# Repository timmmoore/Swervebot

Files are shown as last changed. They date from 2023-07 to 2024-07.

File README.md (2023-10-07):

# Swervebot

https://cad.onshape.com/documents/ee819cf6ea491e04f0fba739/w/47ab37900572e080b95199d2/e/a63b98e65827662d9141c87c

https://cad.onshape.com/documents/98357d3c8f8b098add8002f2/w/b5a1efd9deb641ade0f32837/e/772a9ea7ca7ad6a00d48e67d

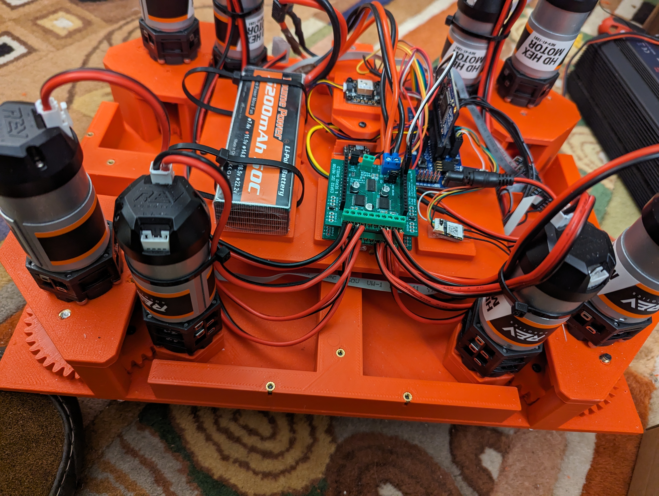
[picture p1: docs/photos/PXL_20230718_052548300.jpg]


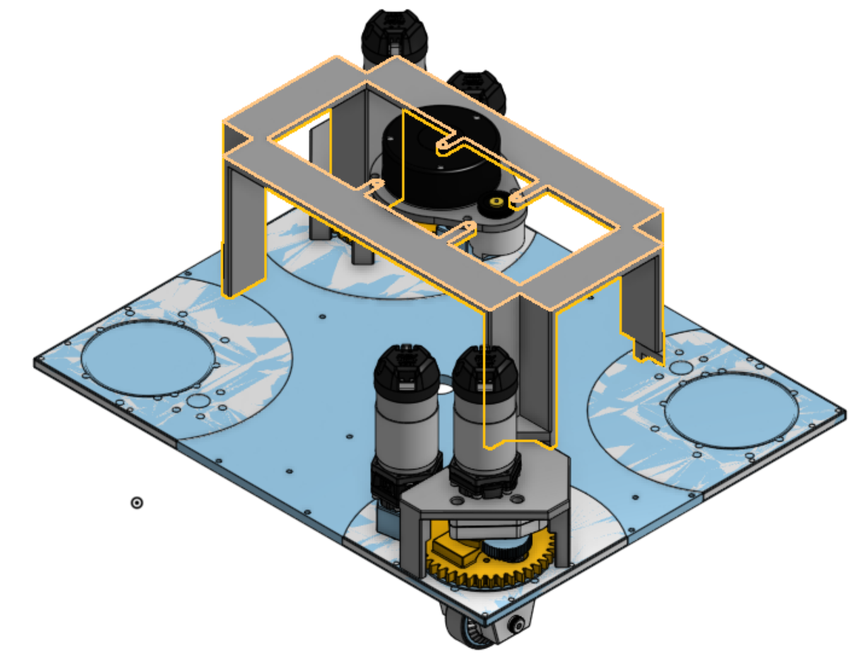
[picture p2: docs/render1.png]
render


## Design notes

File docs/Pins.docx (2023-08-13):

# Pins

SBUS_RX | 7 | Channel data from receiver
S.PORT | 6 | Telemetry to transmitter
SBUS_TX (not used) | 5 | Backup SBUS from 2nd Rx
MOTOR_SDA | 23 | 1MHz I2C for 2 motor drivers 0x40, 0x41
MOTOR_SCL | 22
MOTOR DRIVER FAN | 30
ENCODER1 | 8 | PWM SRX through bore encoder
ENCODER2 | 9
ENCODER3 | 10
ENCODER4 | 11
QUADRATURE 1A | 15 | Encoder on drive motors
QUADRATURE 1B | 14
QUADRATURE 2A | 3
QUADRATURE 2B | 2
QUADRATURE 3A | 13
QUADRATURE 3B | 12
QUADRATURE 4A | 1
QUADRATURE 5B | 0
PMW CS | 19 | Pmw3901 optical flow sensor, SPI
PMW SCK | 18
PMW SDO | 17
PMW SDI | 16
USFSMAX SDA | 21 | 3.4MHz I2C for IMU 0x57
USFSMAX SCL | 20
USFSMAX RESET | -1 | Not used
BATTERY ANALOG | 31 | ADC, resistor divider 8K2+3K
TEMP1 ANALOG | 26 | TMP36 temperature sensors on ADC
TEMP2 ANALOG | 27
TEMP3 ANALOG | 28
TEMP4 ANALOG | 29
GPS SDA | 24 | 1.5MHz I2C 0x10
GPS SCL | 25
SPARE2 | 4
WIFI_RES | 56 | WIFI connection for programming/debug
WIFI_PGM | 57
DEBUG_TX/WIFI_DI | 62
DEBUG_RX/WIFI_DO | 63
SD SDO | 58
SD SDI | 59
SD CS | 60
SD CLK | 61

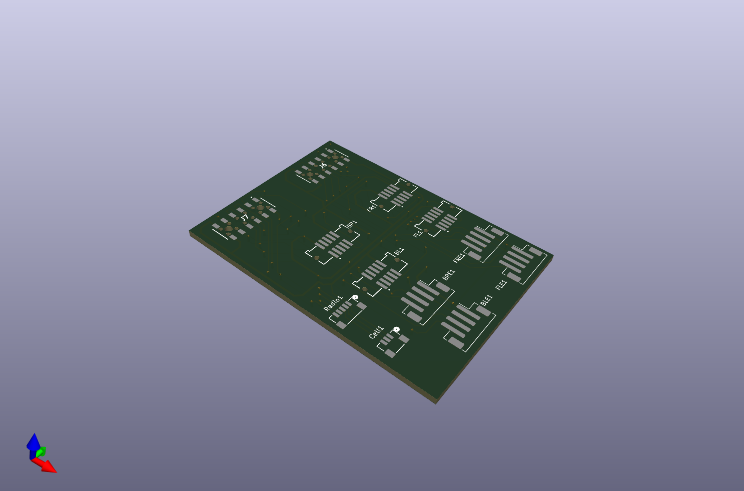
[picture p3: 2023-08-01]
docs/sensor2.png

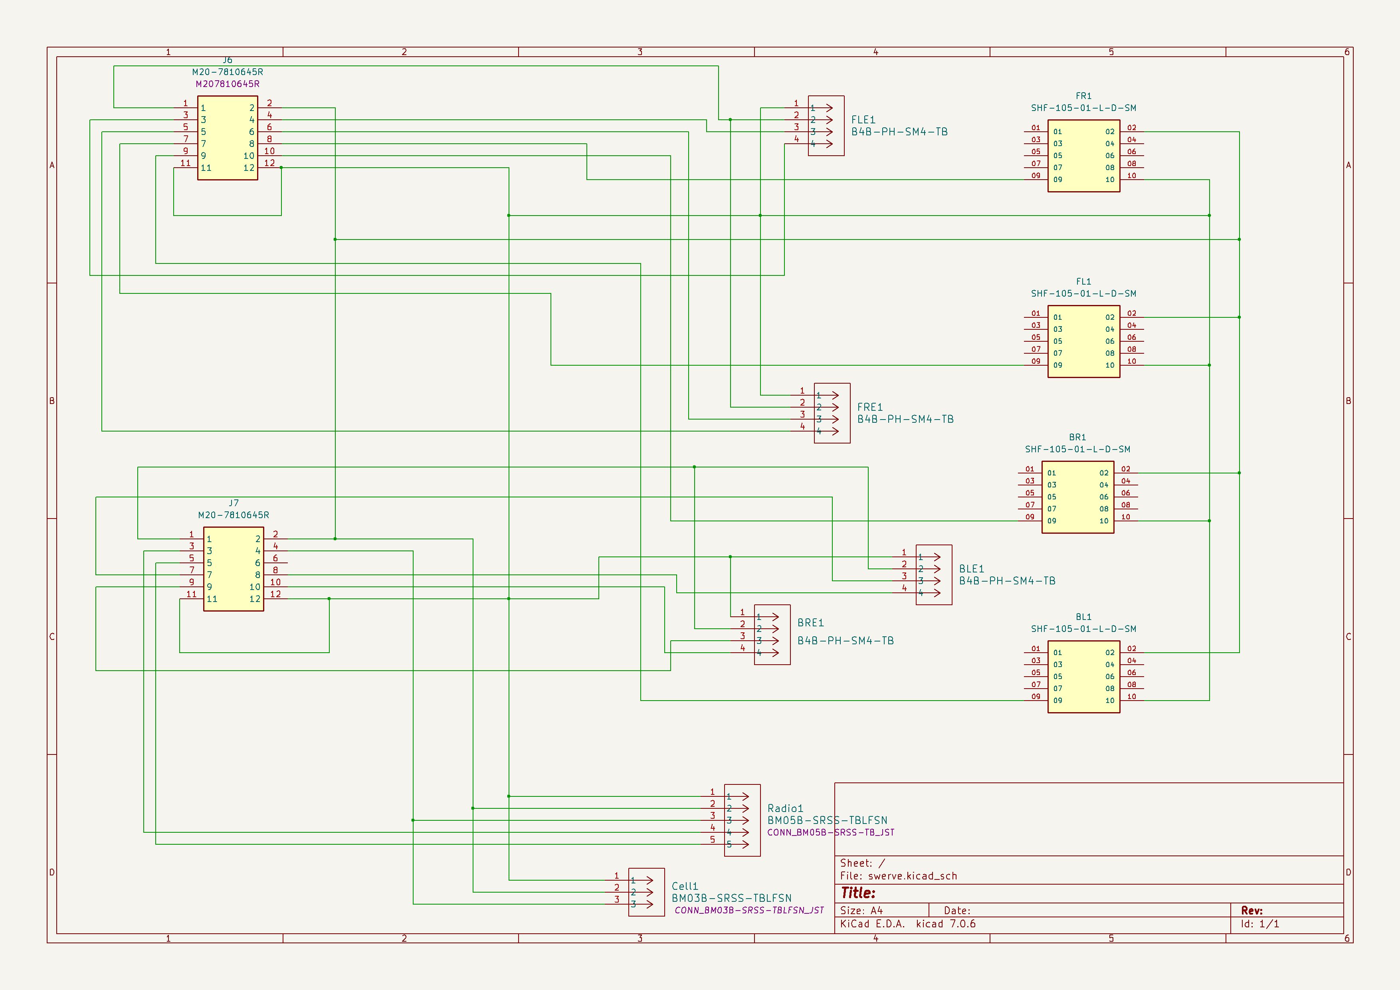
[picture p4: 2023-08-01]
docs/sensorsch2.png

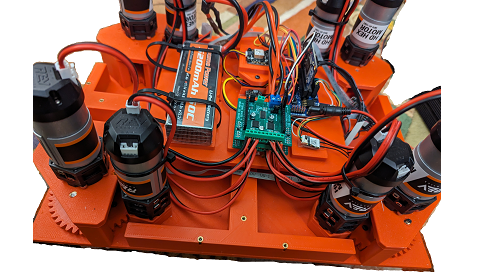
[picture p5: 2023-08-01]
docs/photos/swerve1.png

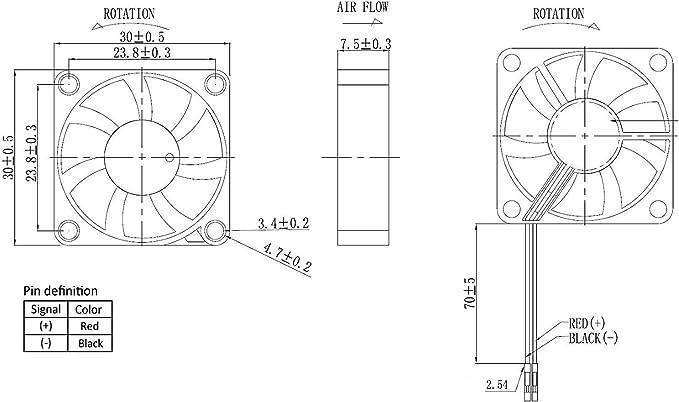
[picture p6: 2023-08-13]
docs/615SG+HSIiL._AC_SX679_.jpg

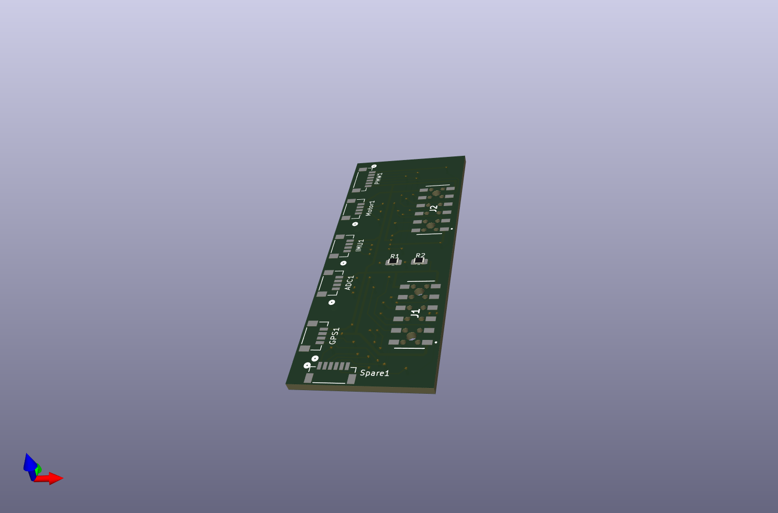
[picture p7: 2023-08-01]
docs/sensor1.png

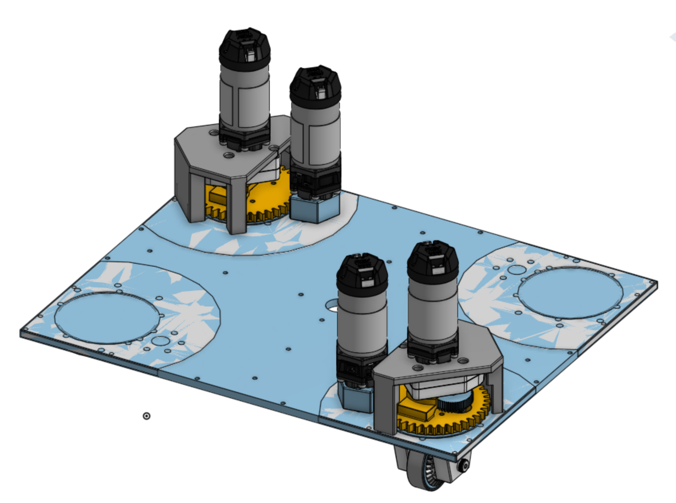
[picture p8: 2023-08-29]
docs/render.png

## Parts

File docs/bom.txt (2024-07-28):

8x	motors			https://www.revrobotics.com/rev-41-1600/						$360
1x	bearing insert		https://www.revrobotics.com/rev-41-1528-pk20/						$10
4x	12 tooth gear		https://www.revrobotics.com/5mm-Metal-Hex-Bore-Gears/					$20
4x	through bore encoder	https://www.revrobotics.com/rev-11-1271/						$192

4x	bevel gear		https://www.gobilda.com/2-1-ratio-bevel-gear-set-8mm-rex-bore-pinion-gear/		$120
4x	gear			https://www.gobilda.com/2303-series-steel-mod-0-8-pinion-gear-8mm-rex-bore-30-tooth/	$40

16x	bearing	8mm		https://www.amazon.com/gp/product/B082PPLHLQ						$19
4x	spacers			https://www.amazon.com/gp/product/B09HSS2TJY						$6.30
4x	shoulder bolt		https://www.amazon.com/gp/product/B09L51S24P						$14
4x	bearing 60mm		https://www.amazon.com/gp/product/B082PSBTLP						$29
	heatset			https://www.amazon.com/dp/B07L96KVP3							$18

1x	battery 3S		https://www.amazon.com/gp/product/B07SYNLFB5						$48/2
1x	5V converter		https://www.amazon.com/gp/product/B08VJ2ZF46

1x	fan			https://www.amazon.com/gp/product/B0792BW2VH
1x	rc receiver		https://www.amazon.com/gp/product/B074QHJRBC
1x	switch			https://www.amazon.com/gp/product/B0BFHZ9XYX

4x	motor drivers		https://www.amazon.com/gp/product/B0C77ZR4Z9						$80

1x	IMU                   	https://www.tindie.com/products/onehorse/usfsmax-module-and-carrier/
1x	GPS                   	https://www.adafruit.com/product/4415
1x	Optical flow		https://shop.pimoroni.com/products/pmw3901-optical-flow-sensor-breakout?variant=27869870358611
4x	TMP36 temp sensor	https://www.amazon.com/gp/product/B07LG758H3/
1x	fan mosfet		https://www.amazon.com/gp/product/B00MMY1WTK

1x	prop2 starter		https://www.parallax.com/product/propeller-2-mini-starter-bundle/

1x	pcbs			pcbs see swervebot/pcb (oshpark.com)

1x 	xrp board		https://www.sparkfun.com/products/22727							$50

using pico expansion board
6 connectors
	GP0, 1
	2, 3
	8, 9
	16, 17
	20, 21
	26, 27

also 4, 5, 6, 7, 10, 11, 12, 13, 14, 15, 18, 19, 22

4x swerve module - 5 pins per module
	2x pwm out (speed control), gnd
	1x pwm in (angle sensor), gnd, +3.3V
	2x quadrature in, gnd, +3.3V

4-6	4pin, quad 0,1
7-11	6pin, quad 2,3
12-14	4pin, quad 8,9
18-20	4pin, quad 16,17	

Use spare 4pin connector for extra gnd/+3.3V, split 4 ways

sensor - 2 pins
	scl - 26, 27 ICL1, gnd, +3.3V

get swerve bot
remove electronics except switch and PSU
Connect +5/gnd to pico via mosfet

add pico expansion board
make cable bundles - 1 per swerve module

xrp firmware
change led and button pins
change i2c pins
change encoder pins
add more motors
change motor pins
change and add more motor channels
change motor code to use servo style pwm on 1 pin
disable rangefinder and linefollower
modify imu code to use sparkfun Odometry sensor

copy xrp example to use swerve drive train

swerve rp2040 QT PY
		I2C in

	out to swerve
		pins 3-6 used to set I2C address - 16, 17, 18, 19 - dupont header
		use bootsel as input to set 0 angle for abs encoder

		encoder		3.3, gnd, A, B		4-pin JST-PH to 4pin dupont connector
		through-bore	5V, gnd, abs		2x5pin to 3pin dupont
							jst-ph 6pin (rev)
		motor driver	gnd, 12v, 2x pwm	4pin dupont to 3pin dupont

		qwiic, cut +V to main pico		qwiic with 3.3 not connected
		5V from main pico
		12V, gnd from main pico to motor driver

		A0, A1 to motor driver
		A2 to through-bore encoder
		SDA, SCL, 3.3V to motor encoder

		5V and gnd to expansion board
		5V to through-bore and main pico
		gnd to through-bore, motor driver and motor encoder

	qt py carrier
		qwiic i2c in to qt py
		power in 12, 5 (14), gnd (13) - 3 pin
		motor driver 2xgnd, 12, 2x pwm (29,28) - 5pin
		encoder 3.3, gnd, a, b (24, 25) - 4pin jst-ph
		throughbore   5V, gnd, pwm (27) - 2x5
			    3.3V, gnd, pwm (27) - 6pin jst-ph
		4pin address header - 3,4; 5,6 - dupont header

pico-w main cpu
	mount 5 qwiic breakout to main board
		4x motor rp2040, 1x odometry board
	mount 5v regulator
		power to pico through diode
		12V, gnd input connector
		4x 2pin 12V, gnd
		4x 1pin 5V, each 5V has diode

xrp-wpilib

servo
gnd, 5v, 16
gnd 5v 17

ultra
gnd 3.3 20 21

line
gnd, 3.3, 26 27

extra
gnd, 3.3, 22, 28

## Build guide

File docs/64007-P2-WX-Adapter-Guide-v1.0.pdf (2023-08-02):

# P2 WX Adapter Add-on Board (#64007)

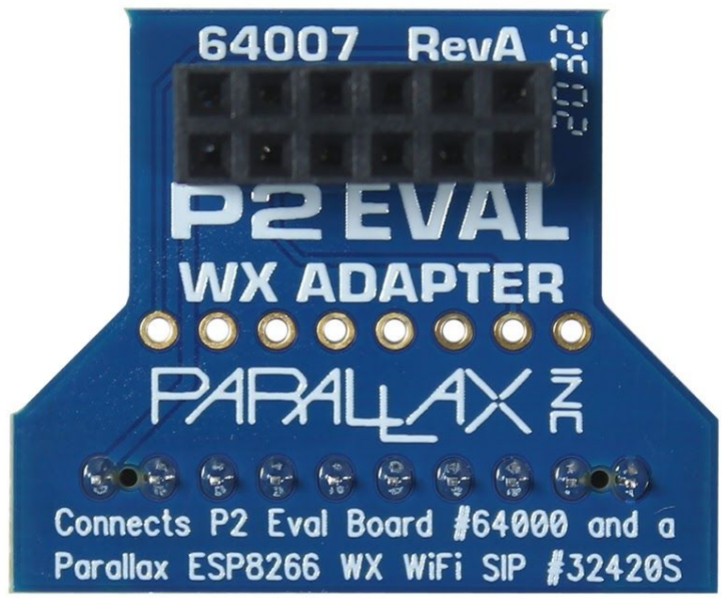
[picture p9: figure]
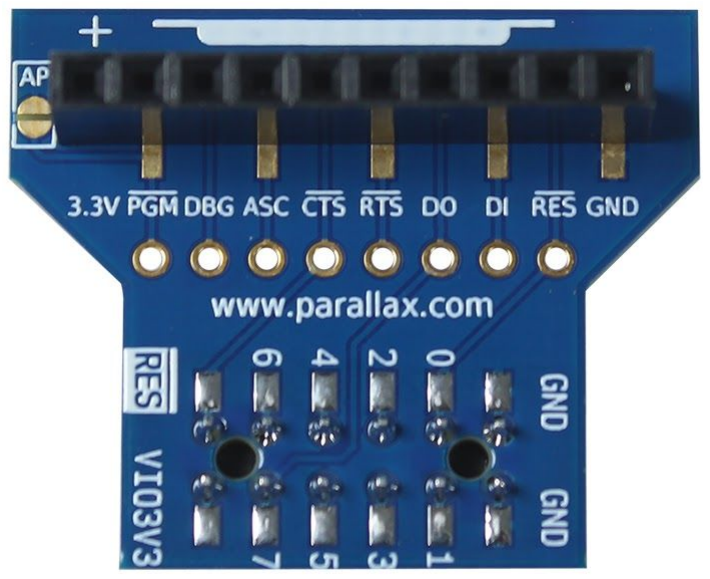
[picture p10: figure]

This adapter provides a convenient way to add wireless programming and serial communication capabilities to the Parallax Propeller P2 microcontroller. The adapter connects a Parallax ESP8266 WX WiFi SIP module to any P2 development board with a standard 2x6 way accessory header.

The WX adapter can be connected to any P2 accessory header for serial-over-WiFi communications. For wireless programming, look for the P56–P63 header marked with the “RES” logo.

Serial-over-WiFi communications from any accessory header is available with any ESP8266 WiFi SIP module firmware version. To add the feature for programming the Propeller 2 wirelessly refer to the instructions for upgrading your ESP8266 WiFi SIP module firmware to the latest version. P2 WiFi firmware has a drag/drop P2 loader on its self-hosted web page, which will accept a P2 program binary file compiled in any language.

### Features

- Connects a Parallax WX WiFi ESP8266 SIP module to the Propeller 2 Accessory Header
- Allows wireless programming when used with an accessory header with the “RES” logo
- Load a binary file created in any P2 programming software to the Propeller 2 over WiFi
- Connect to any 2x6 way accessory header for serial-over-WiFi communication
- Unpopulated pads allow access to all the WiFi module SIP control signals, handy for attaching logic probes.
- Golden Egg shaped Access Point (AP) enable pads.

### Specifications

- 10-pin SIP socket with 0.1" spacing for the Parallax WX WiFi ESP8266 SIP Module (#32420S)
- Unpopulated 8-pin SIP through-hole pads with 0.1” spacing for access to the WiFi module PGM, DBG, ASC, CTS, RTS, DO, DI and RES control signals
- 2x6 female socket with 0.1” spacing compatible with the standard Parallax P2 Accessory sockets
- PCB Dimensions: 1.2 x 1.0 in (30.48 x 25.4 mm)
- Operating temperature: -40 to +185 °F (-40 to +85 °C)
Copyright © Parallax Inc. | P2 WX Adapter Add-on Board (#64007) | v1.0 11/12/2020 Page 1 of 7

Web Store: www.parallax.com

Tutorials: learn.parallax.com

Sales: sales@parallax.com

Tech Support: support@parallax.com

Sales: (888) 512-1024

Educator Hotline: (916) 701-8625

Office: (916) 624-8333

Fax: (916) 624-8003

### Wireless Programming Quick-Start Guide

Items required
- Propeller 2 board with the 2x6 P56–P63 header showing the RES logo
- Parallax WX ESP8266 WiFi Module - SIP, #32420s
- Suitable power supply for your Propeller 2 board
- Computer with wireless network adapter
- Propeller 2 programming software that generates binary files, such as the Propeller Tool 2.3
- Latest P2 firmware and example binary, downloaded from the 64007 product page at www.parallax.com. The file “LED57.binary” will blink an LED connected to P2 I/O pin P57.

Connecting the Hardware
First, connect the Parallax WX ESP8266 WiFi Module - SIP (#32420s) to the P2 WX Adapter (#64007) as shown. The WX Adapter has a white silkscreen marking beside the WiFi module socket which indicates the orientation of the metal can when the WiFi module is inserted.

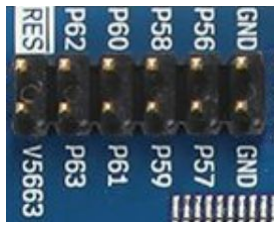
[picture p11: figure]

Then, plug the adapter into the 2x6 header marked RES on your P2 development board. The header must also connect to P2 I/O pins P56–P63, power, and ground as shown below.

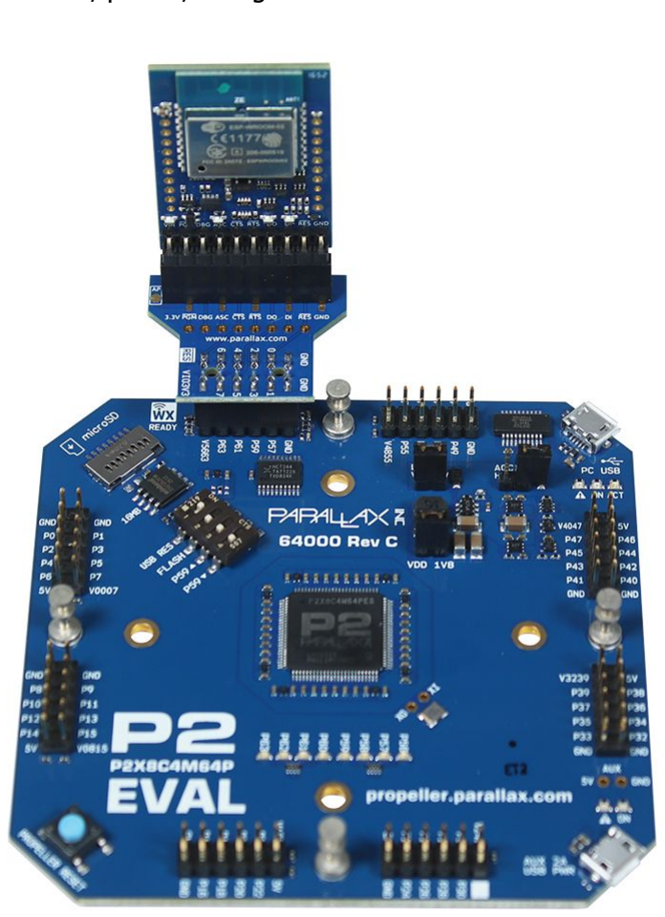
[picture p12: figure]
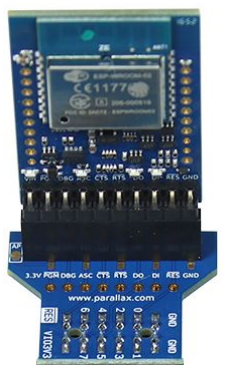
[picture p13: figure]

Copyright © Parallax Inc. | P2 WX Adapter Add-on Board (#64007) | v1.0 11/12/2020 Page 2 of 7

Update the WX WiFi Module Firmware

A. Connect to the WiFi module
1. Connect the Parallax WX ESP8266 WiFi Module to any available accessory header on your Propeller 2 board using the P2 WX Adapter Add-on Board.
2. Power on your Propeller 2 board.
3. Make sure the WiFi module's blue ASC LED starts to blink or light up.
4. From your computer (could be a tablet, laptop or smartphone), search for available WiFi networks and connect to the Parallax WX ESP8266 WiFi module network. By default, the device name will be in this format: WX-123456.
5. If the module is not found when searching for wireless networks, grab a paperclip or similar small metal object and touch 4 times quickly the golden egg on the P2 WX Adapter PCB (labelled AP). You want to short out the 2 pads of the egg 4 times in quick succession. When you are successful you should notice the behaviour of the blue “ASC” LED changes, and from your computer you will be able to search again for new wireless networks until you find the WX-123456 network.
B. One time setup (Ignore this section if previously completed)
1. Once connected to the WiFi module, open your web-browser (Chrome or Edge recommended) and visit this address: http://192.168.4.1
2. You should see the Parallax Wireless Module webpage, with various menus on the left. If the menus are not visible and you are using a small-display device, then you might need to rotate the display to landscape view.
3. Click on the “Firmware” menu on the left-hand-side and upload the special P2 firmware file (P2_httpd_xxxx.ota) downloaded previously. Once completed the module will reboot; allow time for the module to reboot and re-connect your laptop WiFi connection if necessary.

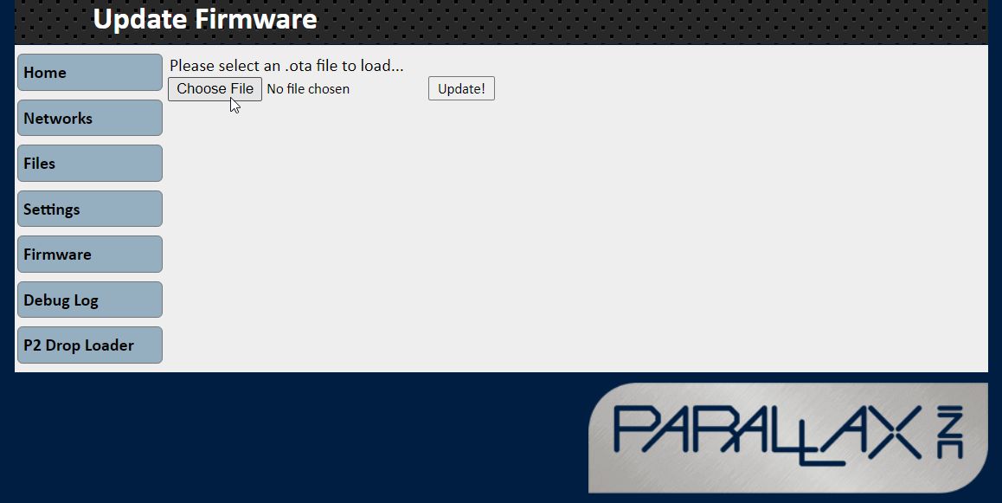
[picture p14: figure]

Copyright © Parallax Inc. | P2 WX Adapter Add-on Board (#64007) | v1.0 11/12/2020 Page 3 of 7

4. Again, visit the webpage at : http://192.168.4.1 and click on the “Settings” menu on the left-hand-side.

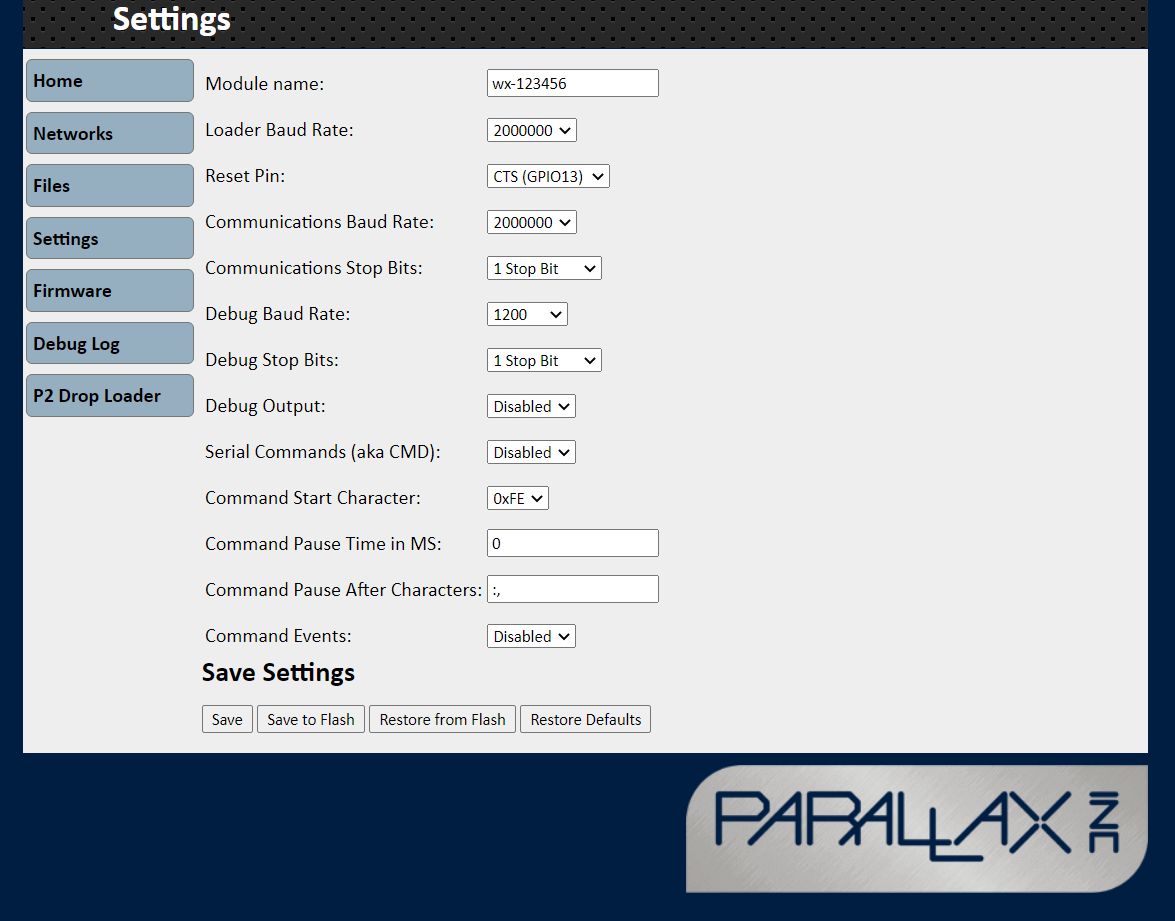
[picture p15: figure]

5. The reset dropdown option should be set to “CTS”. (It might be DTR by default). Once set to “CTS”, then click the “SAVE” and “SAVE to FLASH” buttons at the bottom of the page.
6. If your firmware update was successful, you will see a new menu on the left-hand-side “P2 Loader”. If not, try holding SHIFT and pressing F5 to force your browser to clear its cache and refresh the page.
C. Using the P2 Loader to wirelessly program your P2 microcontroller
1. Ensure you have completed the steps in section A. Connect to the WiFi module, and then ensure the WX Adapter is plugged into the appropriate accessory header of your Propeller 2 development board for wireless programming. The appropriate accessory header to use for wireless programming is marked with a “RES” logo, as seen in the image in the above Items required section.
2. Once connected to the WiFi module, open your web-browser (Chrome or Edge recommended) and visit this address: http://192.168.4.1
3. Click on the “P2 Drop Loader” menu on the left-hand-side..
Copyright © Parallax Inc. | P2 WX Adapter Add-on Board (#64007) | v1.0 11/12/2020 Page 4 of 7

4. Once the web-page has loaded (which may take a few seconds the first time), you will see a drag/drop area. To wirelessly program the connected P2 microcontroller, drag/drop P2 binary files to this area from a folder on your computer.
5. The upload will happen very quickly, and when successful the webpage will report the status message “Done!”.

Tip! If uploading the LED blink demo, ensure you have the P2 Edge Module “LED” dip-switch turned on!

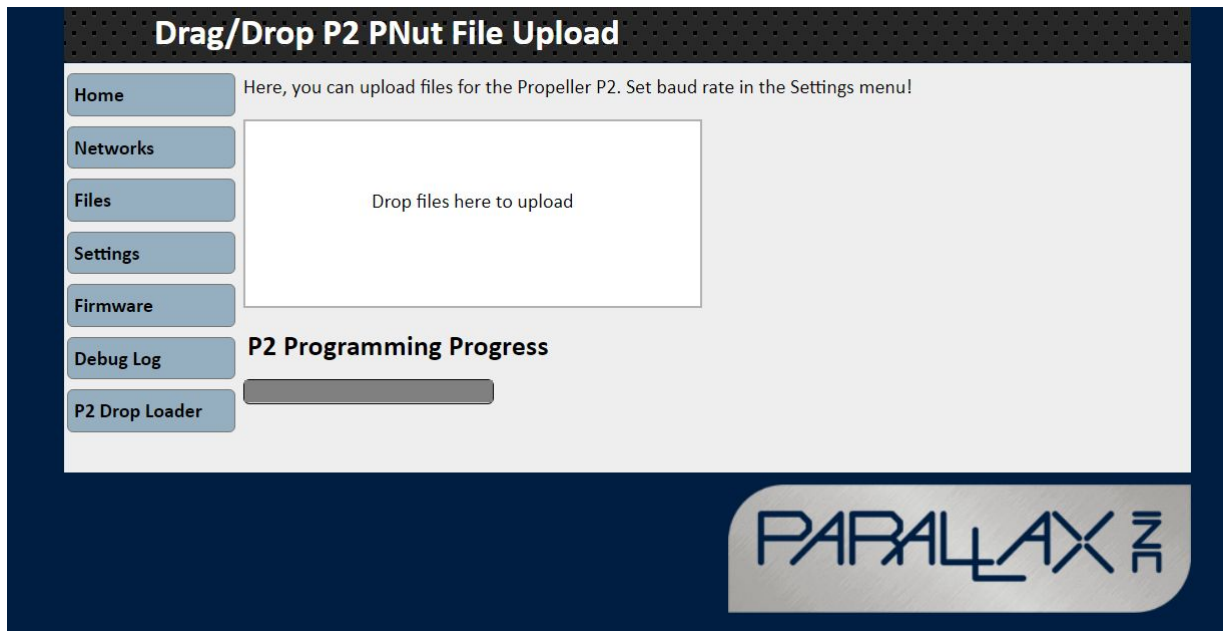
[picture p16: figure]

Copyright © Parallax Inc. | P2 WX Adapter Add-on Board (#64007) | v1.0 11/12/2020 Page 5 of 7

### Pin Connections

Pin connection diagram: Dark blue traces on top of PCB, light blue on bottom of PCB

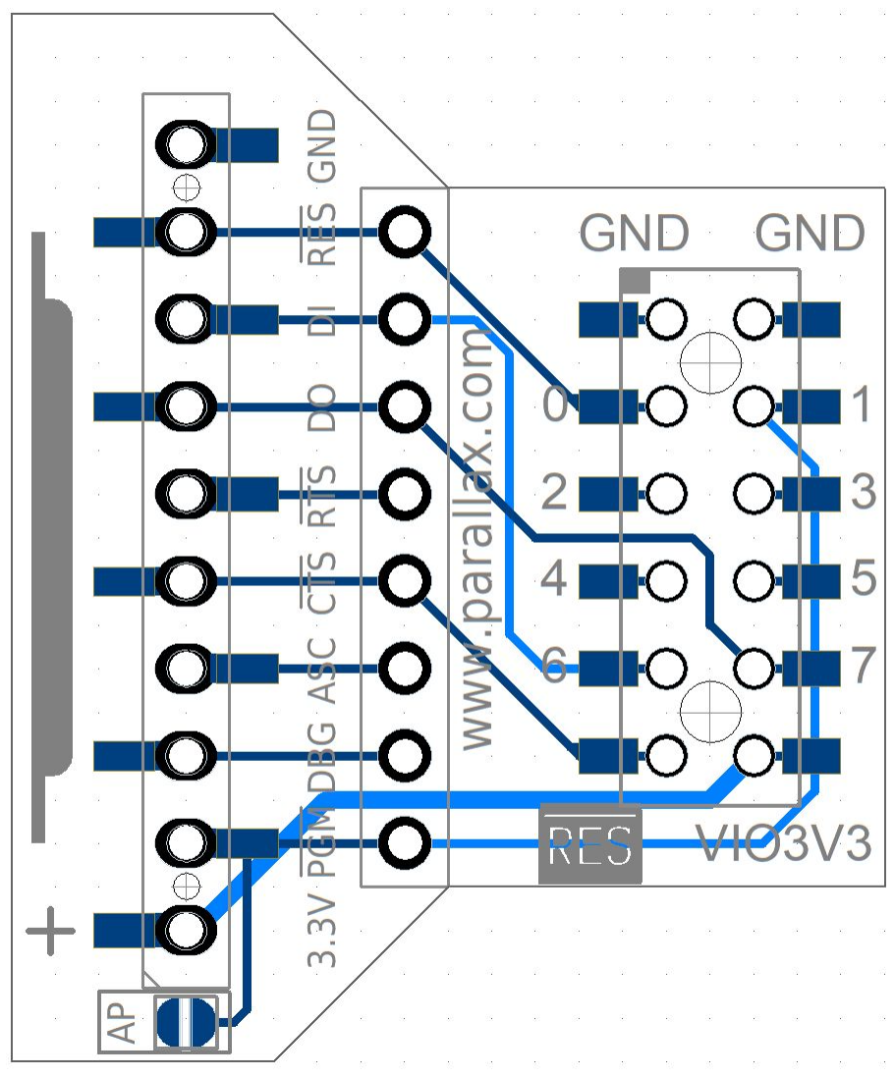
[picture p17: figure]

Copyright © Parallax Inc. | P2 WX Adapter Add-on Board (#64007) | v1.0 11/12/2020 Page 6 of 7
Accessory header pin | WiFi module pin | Function
GND | GND | Common ground
0 | RES | WiFi module reset signal
1 | PGM | WiFi module configure (ESP IO0)
2 - 5 | - | Not Connected
6 | DI | WiFi module RXD
7 | DO | WiFi module TXD
RES | CTS | Target board reset signal for Propeller microprocessor (ESP IO13)
VIO3V3 | 3.3V | Supply voltage to WiFi module

### Dimensions

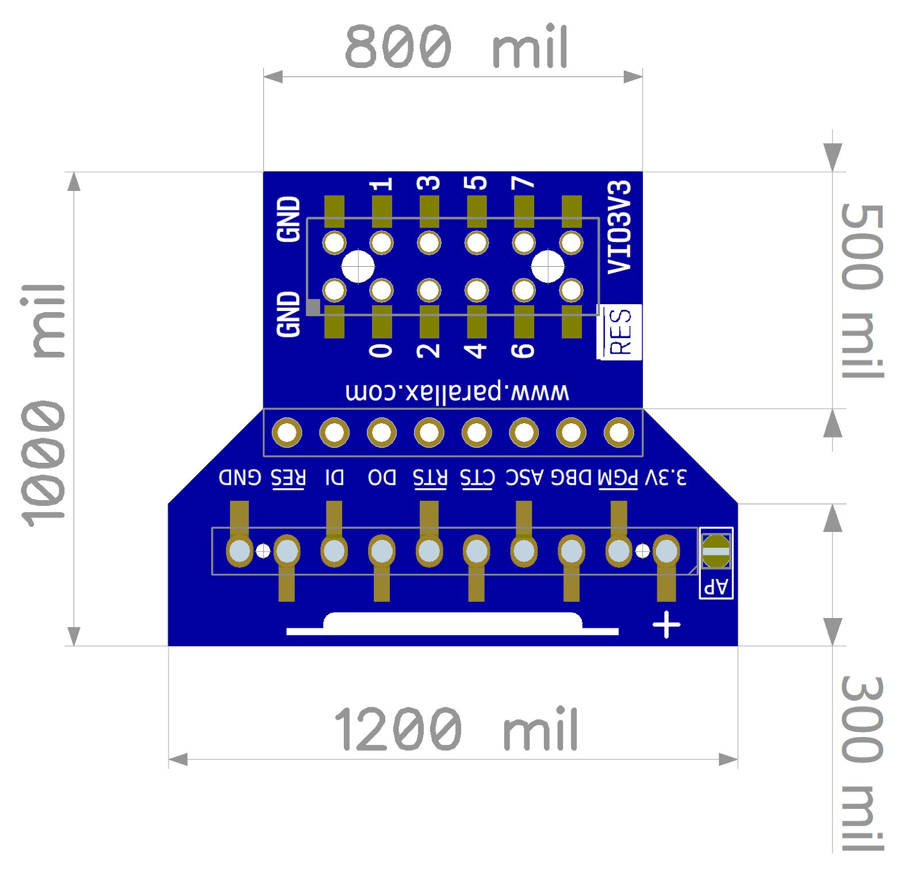
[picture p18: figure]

### Resources and Downloads

Check for the latest version of this document and the schematic diagram from the P2 WX Adapter product page. Go to www.parallax.com and search 64007.

### Revision History

Version 1.0: Original release.

Copyright © Parallax Inc. | P2 WX Adapter Add-on Board (#64007) | v1.0 11/12/2020 Page 7 of 7

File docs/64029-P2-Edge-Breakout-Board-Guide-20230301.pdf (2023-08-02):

Web Store: www.parallax.com Tutorials: learn.parallax.com
Sales: sales@parallax.com
Tech Support: support@parallax.com

Sales: (888) 512-1024
Educator Hotline: (916) 701-8625 Office: (916) 624-8333
Fax: (916) 624-8003

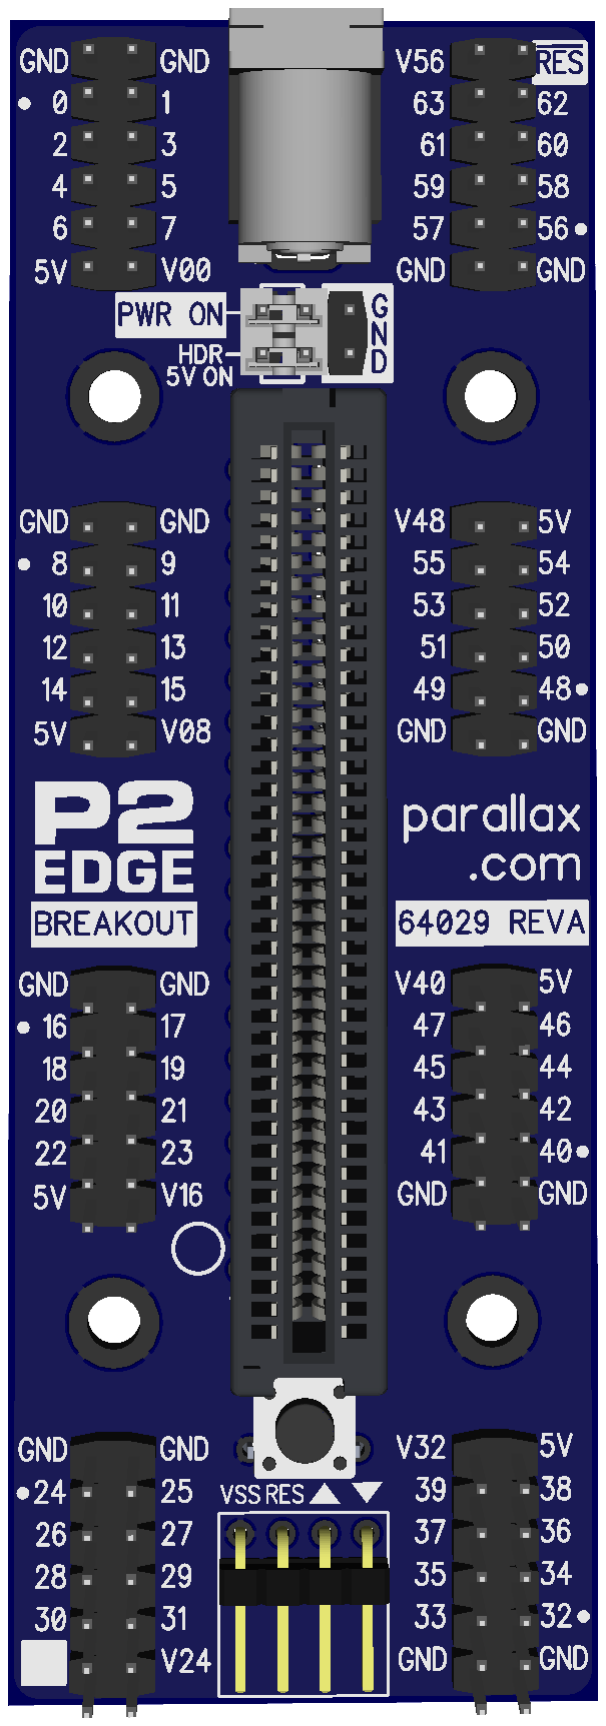
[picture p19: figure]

# P2 Edge Breakout Board (#64029)

The P2 Edge Breakout Board provides a compact interface to the P2 Edge Module for experimenting and developing with the Propeller 2 microcontroller.

The board accepts the P2 Edge Module (#P2-EC) and includes a supply voltage DC Jack socket, power headers, Parallax Prop Plug (#32201) programming header, and reset button.

All 64 of the P2 Edge Smart I/O pins are available at eight 0.1” pin header sockets, compatible with both single and dual header Propeller 2 accessories. All accessory headers are arranged to accept single or dual P2 accessory boards. The last header includes the programming and memory pins (58-63) and reset signal (RES) for wireless programming when using the P2 WX Adapter (#64007) with Parallax WX ESP8266 SIP module (#32420S).

## Features

- Vertical socket for the Parallax P2 Edge Module (#P2-EC)
- Solder-free prototyping, header sockets for power, programming and I/O
- Center-positive 2.1 mm barrel jack for external 5 VDC power supply
- Flexible 0.1” 2x3 way power header allows use of an external switch or power supply
- Convenient reset button
- All 64 Smart I/O pins brought out to 0.1” 2x6 way P2 accessory headers
- Dedicated Parallax Prop Plug (#32201) header, for system programming and debugging

## Key Specifications

- Voltage input requirements: 5 VDC, absolute maximum 5.5 VDC
- Input Current requirements:
- Recommended minimum 100 mA
- Maximum according to customer application
- VIO Power Supplies: 3.3 V up to 300 mA per 8 I/O pins; requires P2 Edge Module
- Smart I/O pins: 3.3 V logic level, source or sink 30 mA per I/O pin
- USB programming: Serial up to 2 MBaud; requires Prop Plug (#32201) programming adapter
- Wireless programming: (up to 2 MBaud); requires P2 WX WiFi Adapter (#64007) and WX WiFi SIP module (#32420S)
- Mounting holes: Four 3.2 mm diameter plated mounted holes connected to GND
- Operating temperature: -40 to +185 °F (-40 to +85 °C)
- PCB Dimensions: 4 x 1.4 in (101.6 x 35.6 mm)
Copyright © Parallax Inc. | P2 Edge Breakout Board (#64029) | v1.0 03/01/2023 Page 1 of 11

## Orientation

When connecting your P2 Edge Module to the P2 Edge Breakout Board, ensure that the module is inserted with the orientation hole on the module closest to the white orientation circle that is marked on the breakout PCB, close to the bottom-left side of the Edge Socket. Correct module orientation is shown in this image:

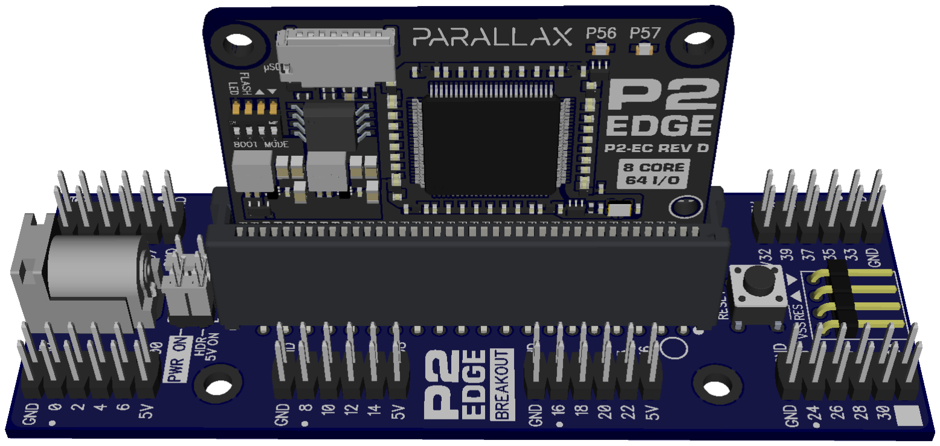
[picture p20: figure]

Copyright © Parallax Inc. | P2 Edge Breakout Board (#64029) | v1.0 03/01/2023 Page 2 of 11

## Compatible Products

See the Propeller 2 section of the Parallax web store for all of the products listed below. Recommended Parts for Getting Started

- P2 Edge Module (#P2-EC)
- P2 Edge Breakout Board (#64029)
- Cable, USB A to DC 2.1mm Jack (#805-00019)
- Breadboard (#700-32023)
- 200mm Jumper Wires, MF 40-piece Ribbon (#800-00064)
- 100mm Jumper Wires, MM 40-piece Ribbon (#800-00065)
- Prop Plug programming tool (#32201)
- USB A to Micro B Cable (#805-00016)

Add Wireless Programming & Serial Communication

- P2 to WX Adapter (#64007)
- Parallax WX ESP8266 WiFi Module - SIP (#32420S)

Add Click / mikroBUS development

The P2 to MicroBUS Click Adapter provides developers with connectivity to over 900 different mikroE Click modules for rapid development. Check out the Parallax webshop or your local distributor.

- P2 to MicroBUS Click Adapter (#64008)

Parallax Add-on Boards

These boards fit directly on the 2x6 accessory headers with no need for additional adapters:

- P2-ES Eval Board Accessory Set (#64006-ES). Set of eight, with pushbuttons, serial host, LED matrix, HDMI output, prototyping, serial device, Goertzel HID, and A/V breakout.
- HyperRAM & HyperFLASH Add-On (#64004-ES)
- Protoboard Add-on (#64005-ES)
- P2 microSD Add-on Board (#64009)
- Universal Motor Driver P2 Add-on Board (#64010)
- P2 RTC Add-on Board (#64013)
- P2 HD Audio Add-on Set (#64014)
- P2 Eval HUB75 Adapter Board (#64032)

For the latest selection of Development and Add-on Boards, refer to your local Parallax distributor or Propeller 2 shop at www.parallax.com.

Copyright © Parallax Inc. | P2 Edge Breakout Board (#64029) | v1.0 03/01/2023 Page 3 of 11

## Feature Descriptions

Read the full explanation of each labeled feature on the pages that follow this diagram.

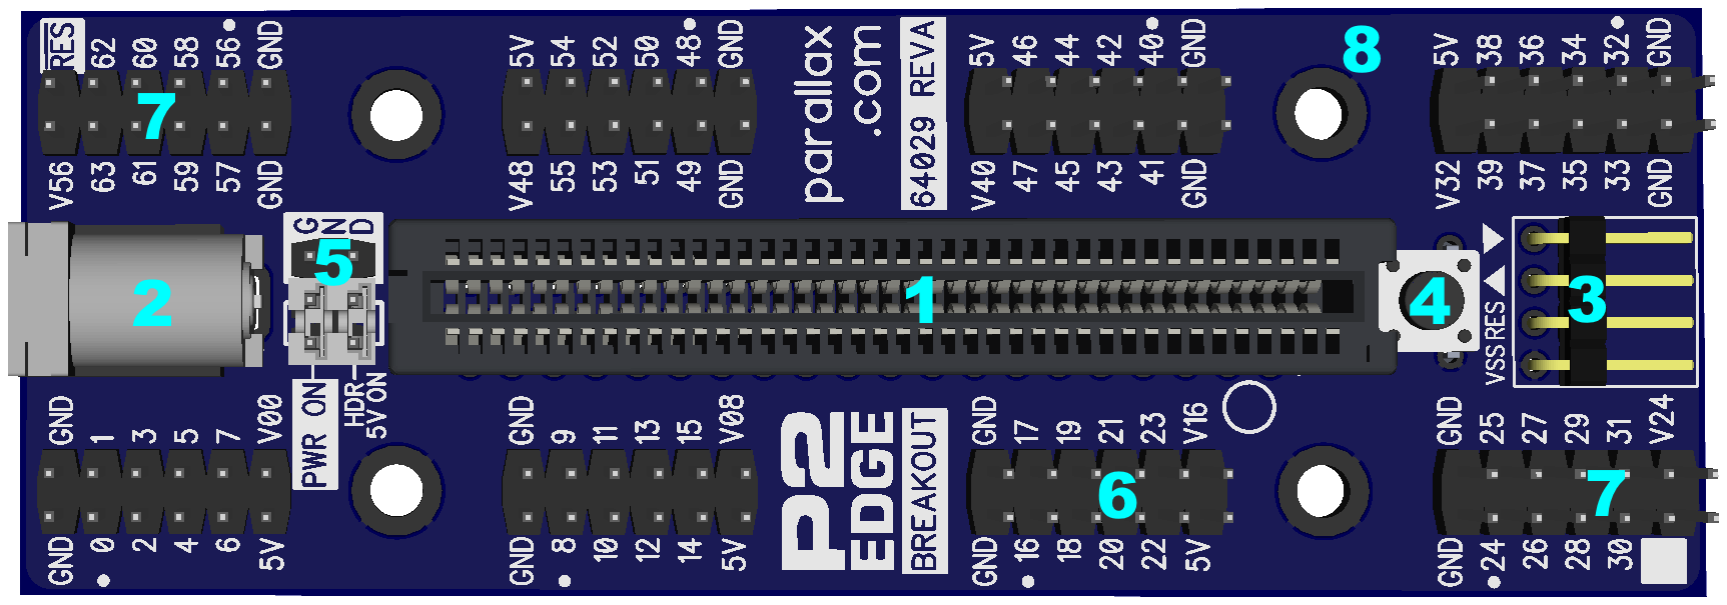
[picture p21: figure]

### 1. Parallax P2 Edge Module Socket

The P2 Edge Module socket is a 0.05 in (1.27 mm) pitch, 80-way vertical socket. Refer to Edge Connector Pin Assignments in the P2 Edge Module product guide for full details.

The P2 Edge Module must be inserted with its orientation hole closest to the RESET Button, and aligned with the white orientation ring that is marked on the breakout board.

CAUTION! The P2 Edge Module power input pads have reverse polarity protection, but damage could occur from user circuits attached to the IO pins incorrectly, so care should always be taken to ensure correct orientation.

### 2. Power Jack

The 2.1 mm center-positive DC power barrel jack socket accepts 5 VDC only. To provide power we recommend the Parallax USB A to DC Jack Cable (#805-00019) This will allow you to power the P2 Edge Breakout Board from a computer USB port or hub. For higher current applications, connect the same cable to the Parallax USB Mains Adapter (#750-00001).

CAUTION! Always use a well-regulated power supply and do not exceed 5.5 VDC input!

Copyright © Parallax Inc. | P2 Edge Breakout Board (#64029) | v1.0 03/01/2023 Page 4 of 11

### 3. Prop Plug Programming Header

The P2 Edge Module is programmed by the Parallax Prop Plug programming tool (#32201). To accommodate the Prop Plug, there is a dedicated 4-pin programming and debugging header. The pins are marked ▽ △ RES VSS, and correspond to the pin labeling on the Prop Plug adapter.

Connect the Prop Plug to your computer with a suitable USB cable. Then, insert the Prop Plug onto the header pins with the Prop Plug components facing upward. The upward orientation allows you to see the RX and TX activity LEDs on the Prop Plug while programming or debugging data is being transmitted.

### 4. Reset Button

Use this button to restart the Propeller 2 microcontroller’s program running on the P2 Edge Module. Press and hold to keep the microcontroller in reset. Press and release to reset, load and run the program in EEPROM.

### 5. Power Header

The 0.1” pitch 2x3 way power header comes with two pre-installed 2-pin shunts to enable power to the breakout board.

To disable power to the entire board, remove the top “PWR ON” jumper.

To disable power only for the accessory header 5V pins, remove the bottom “HDR 5V ON” jumper.

Each jumper could be replaced with a switch or could be used to supply power directly to the breakout board (instead of using the DC Barrel
Jack). This is an unsupported customer option -
please refer to the silk labeling on the bottom of the

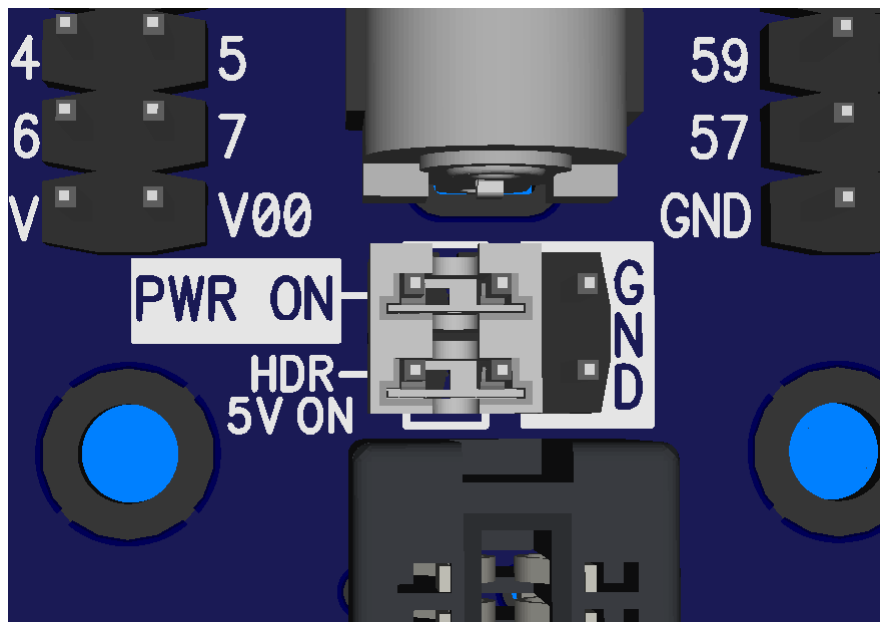
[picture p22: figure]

breakout board and the schematic for further information.

PRO TIP: REMOVE THE HDR 5V ON JUMPER IF YOU ARE NOT USING THE 5V SUPPLY AT THE 2X6 WAY ACCESSORY HEADERS. Doing so will reduce the risk of accidentally causing damage during experimentation; for example, should one of the 5V pins be accidentally connected to a signal or ground pin. All I/O signal pins are rated for 3.3V only!

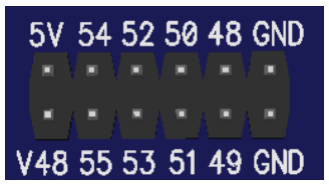
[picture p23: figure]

### 6. I/O Pin Accessory Headers (with 5V output)

With the P2 Edge Module plugged in, each of the Propeller 2's 64 smart I/O pins connect to an accessory header, in specific groups of eight.

Each edge header provides two GND connections, a Vxx output pin supplying the voltage from the corresponding 3.3 V LDO voltage regulator (described here), and optionally a 5 V output that is
connected via the Power Header directly to the Power Jack.
Copyright © Parallax Inc. | P2 Edge Breakout Board (#64029) | v1.0 03/01/2023 Page 5 of 11

DO NOT APPLY VOLTAGE TO THE Vxx Pin; it is a voltage output! Be aware that some I/O pins are also connected to other peripheral circuits; see the Edge Connector Pin Assignments section.

5V OUTPUT VOLTAGE IS PROVIDED TO POWER EXTERNAL ACCESSORIES & SENSORS. DO NOT CONNECT 5V DIRECTLY TO ANY OF THE P2 SMART I/O PINS!

ALL I/O PINS OPERATE AT 3.3V LOGIC LEVEL AND ARE NOT 5V TOLERANT !

### 7. I/O Pin Breakout Edge Headers (without 5V output)

There are two edge headers that do not have 5V routed to them, one for P24-–P31, and one for P56–P63.

The P24–P31 header is marked with a white silk square for the pin beside the Vxx pin. This unlabelled pin is unconnected, but may be
used for connecting a user signal or voltage to a user accessory
board or prototype board.

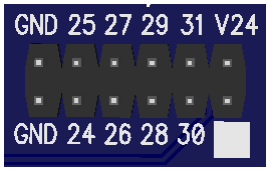
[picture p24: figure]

The P56–P63 header is marked with the RES pin label beside the V56 pin.

The RES pin is active low, and is connected to the Propeller 2 microcontroller RESn circuit on the P2 Edge Module. Momentarily set this pin low to reset the Propeller 2.

The P56–P63 header accepts the the Parallax P2 WX Adapter (#64007) with the Parallax ESP8266 SIP WiFi module (#32420S) in order to program the Propeller 2 wirelessly.

### 8. Mounting Holes

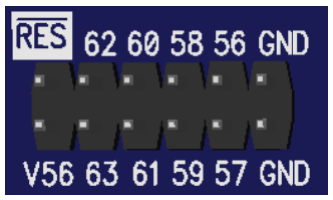
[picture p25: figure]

The four plated mounting holes are attached to the ground plane. See the PCB Dimensions (https://docs.google.com/document/d/15FXvm2-2GxBi8XHcfKeDlXznptRxweGQ6upv5ITP_OA/edit) section for mounting hole dimensions, positions and spacing.

### VIO 3.3V Power and Ground (GND) access

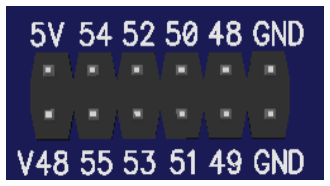
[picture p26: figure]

The positive 3.3 V supply sockets and ground sockets are positioned around the board at the 2x6 way P2 accessory headers. The headers are compatible with the Parallax P2 accessory boards, or use jumper wires to connect the header pins to an external circuit- for example, to a breadboard.

Each group of 8 smart I/O pins has its own 3.3 V low-noise regulator,
with short-circuit and over-current protection. You may see this
Copyright © Parallax Inc. | P2 Edge Breakout Board (#64029) | v1.0 03/01/2023 Page 6 of 11

voltage referred to as VIO (Voltage for IO), and is labeled beside each group of I/O pins in the format Vxx.

The two digits after the V refer to the first of 8 I/O pins that the LDO provides power to. For example in the image, V48 would mean VIO voltage for I/O pins 48 to 55.

Warning: DO NOT join the Vxx pins together. The voltage output is intended to provide logic level and low current supply only to the corresponding group of 8 I/Os (Maximum 30mA per pin, 300 mA total). If a larger current or common supply is required, use an alternative power source such as the Parallax Power Pal (#32133).

Copyright © Parallax Inc. | P2 Edge Breakout Board (#64029) | v1.0 03/01/2023 Page 7 of 11

## Propeller 2 Physical Pins

The Propeller 2 physical pins are shown below. See the Propeller 2 documentation at www.parallax.com for more information about this device. Below, see the Edge Connector Pin Assignments section for details on how they are used on the P2 Edge Module.

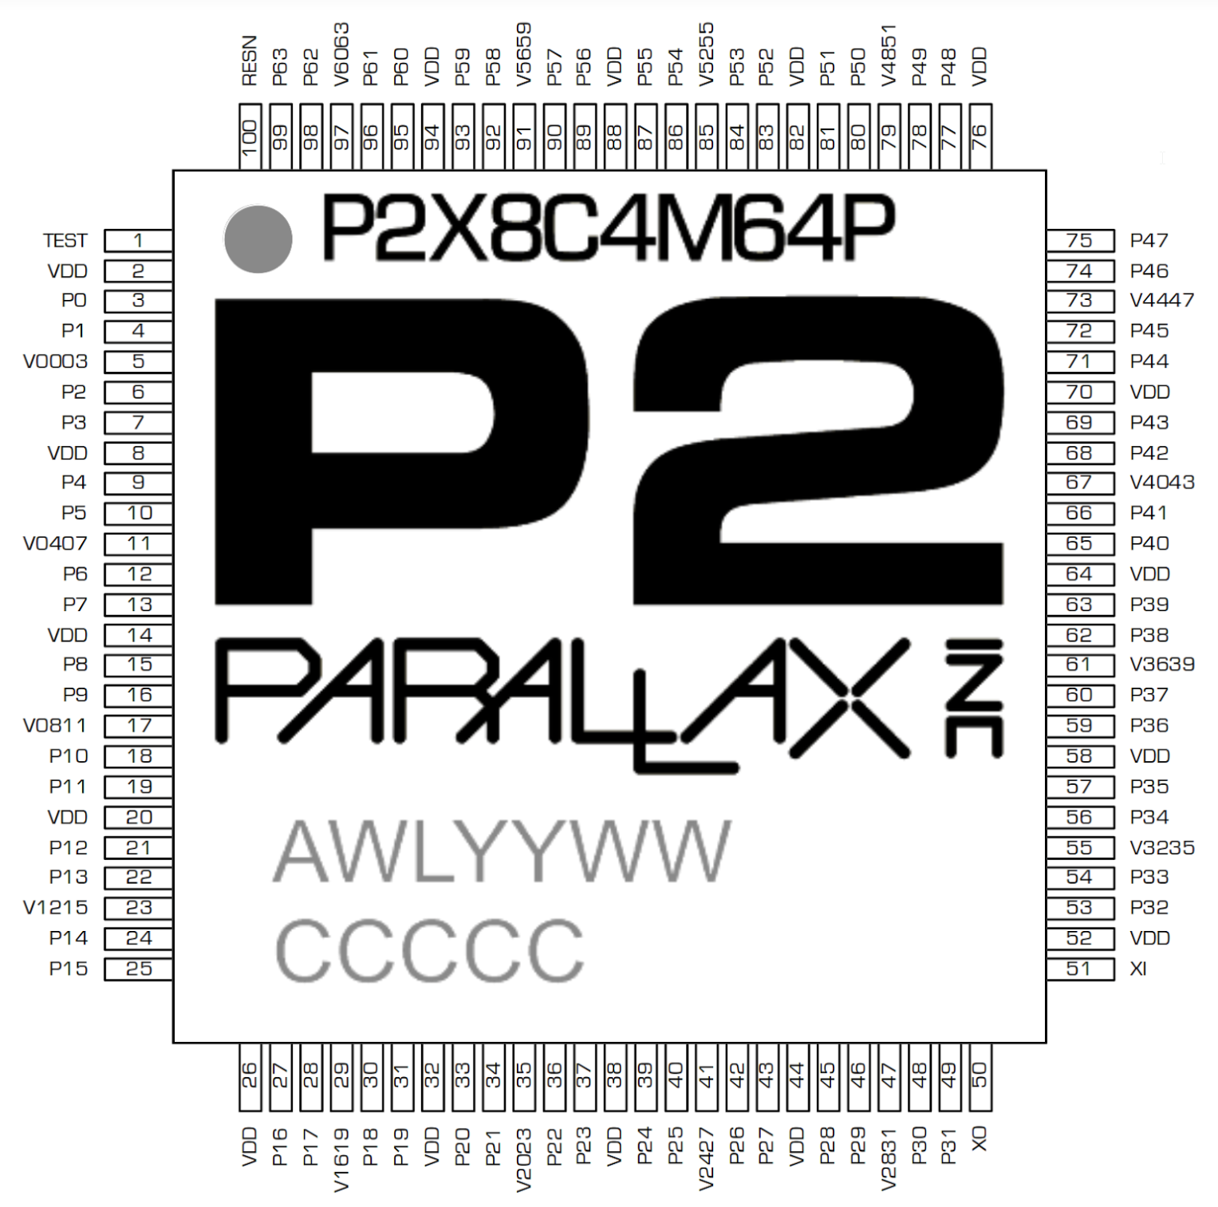
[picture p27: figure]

Copyright © Parallax Inc. | P2 Edge Breakout Board (#64029) | v1.0 03/01/2023 Page 8 of 11

## Edge Connector Pin Assignments

Smart I/O pins P0–P55 are fully free; P56–P63 are routed to peripheral circuits and/or have special P2 boot sequence related functions. See the Propeller 2 documentation at www.parallax.com for full details of P2 smart I/O pin capability.

I/O Pin | Description
P0-P7 | Smart I/O pins, 3.3 V logic level, source or sink 30 mA per I/O pin. On-board LDO regulator supplies 300 mA total, shared by this I/O pin group and edge connector pin V00.
P8-P15 | Smart I/O pins, 3.3 V logic level, source or sink 30 mA per I/O pin. On-board LDO regulator supplies 300 mA total, shared by this I/O pin group and edge connector pin V08.
P16-P23 | Smart I/O pins, 3.3 V logic level, source or sink 30 mA per I/O pin. On-board LDO regulator supplies 300 mA total, shared by this I/O pin group and edge connector pin V16.
P24-P31 | Smart I/O pins, 3.3 V logic level, source or sink 30 mA per I/O pin. On-board LDO regulator supplies 300 mA total, shared by this I/O pin group and edge connector pin V24.
P32-P39 | Smart I/O pins, 3.3 V logic level, source or sink 30 mA per I/O pin. On-board LDO regulator supplies 300 mA total, shared by this I/O pin group and edge connector pin V32.
P40-P47 | Smart I/O pins, 3.3 V logic level, source or sink 30 mA per I/O pin. On-board LDO regulator supplies 300 mA total, shared by this I/O pin group and edge connector pin V40.
P48-P55 | Smart I/O pins, 3.3 V logic level, source or sink 30 mA per I/O pin. On-board LDO regulator supplies 300mA total, shared by this I/O pin group and edge connector pin V48.
P56-P63 | Smart I/O pins, 3.3 V logic level, source or sink 30 mA per I/O pin. On-board LDO regulator supplies 300 mA total, shared by this I/O pin group and edge connector pin V56.
| Alternative functions for P56-P63 (On board the #P2-EC Edge Module)
P56 | Buffered LED
P57 | Buffered LED
P58 | Flash SPI DO (MISO)
P59 | Flash SPI DI (MOSI)
P60 | Flash SPI CLK
P61 | Flash SPI CS
P62 | Prop-Plug RXD (P2 TXD)
P63 | Prop-Plug TXD (P2 RXD)
Other | Description
RESn | Internally pulled up to 3.3V with 10K resistor. P2 will reset when RESn is driven low.
5V | Power input pins for the Edge Module. Connect both 5V edge connector pads to a good quality 5VDC supply. The supply voltage MUST NOT exceed 5.5V! Recommended minimum supply current 100mA, up to 3A for heavy load and multi-cog use.
GND | Provides common signal and supply voltage ground. Connection of all three edge connector GND pads to a solid ground plane on an external layer is recommended.
NC | Not Connected, reserved for future use. Recommended “Do Not Connect” in designs.
Copyright © Parallax Inc. | P2 Edge Breakout Board (#64029) | v1.0 03/01/2023 Page 9 of 11

### Programming Software

Propeller Tool is our recommended tool for programming the P2 Edge Module in SPIN and PASM languages. Other programming languages are possible using third party tools, such as C, BASIC, Forth.

You can find links to the latest tools at the P2 Edge Module product page. Visit https://www.parallax.com and search for “P2-EC.”

### Resources and Downloads

Check for the latest version of this document, free software, and example programs from the P2 Edge Breakout Board product page. Go to www.parallax.com and search 64029.

### Recommend and Absolute Maximum Ratings

Symbol | Quantity | Recommended | Maximum | Units
5 VDC | DC Barrel Jack Supply Voltage † | 5 | 5.5 | V
P0 - P63 | Any I/O Pin | 3.3 | 3.6 | V
P0 - P63 | Source or sink current per I/O pin | | 30 | mA
RESn | Reset input, active low | 3.3 | 3.6 | V

### P2 Edge Socket Pinout (PCB Bottom View)

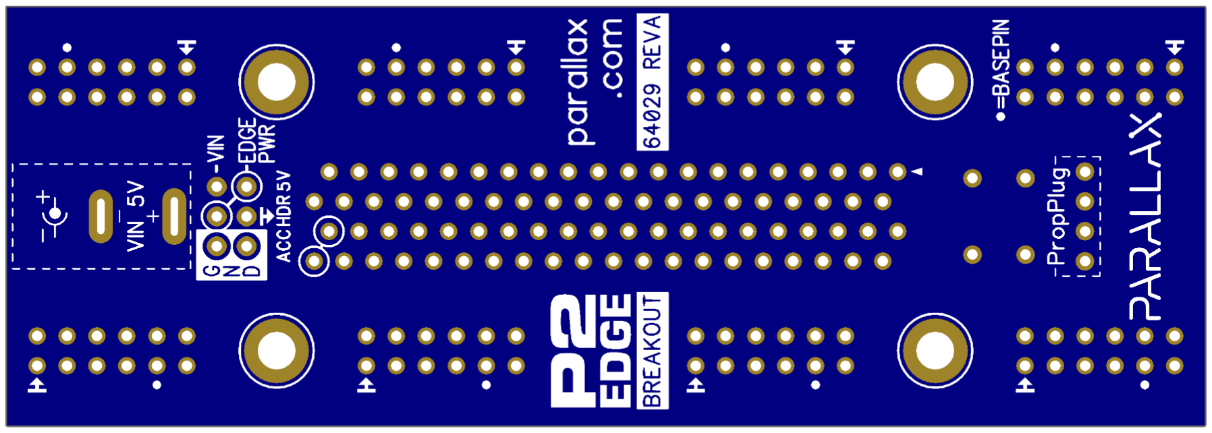
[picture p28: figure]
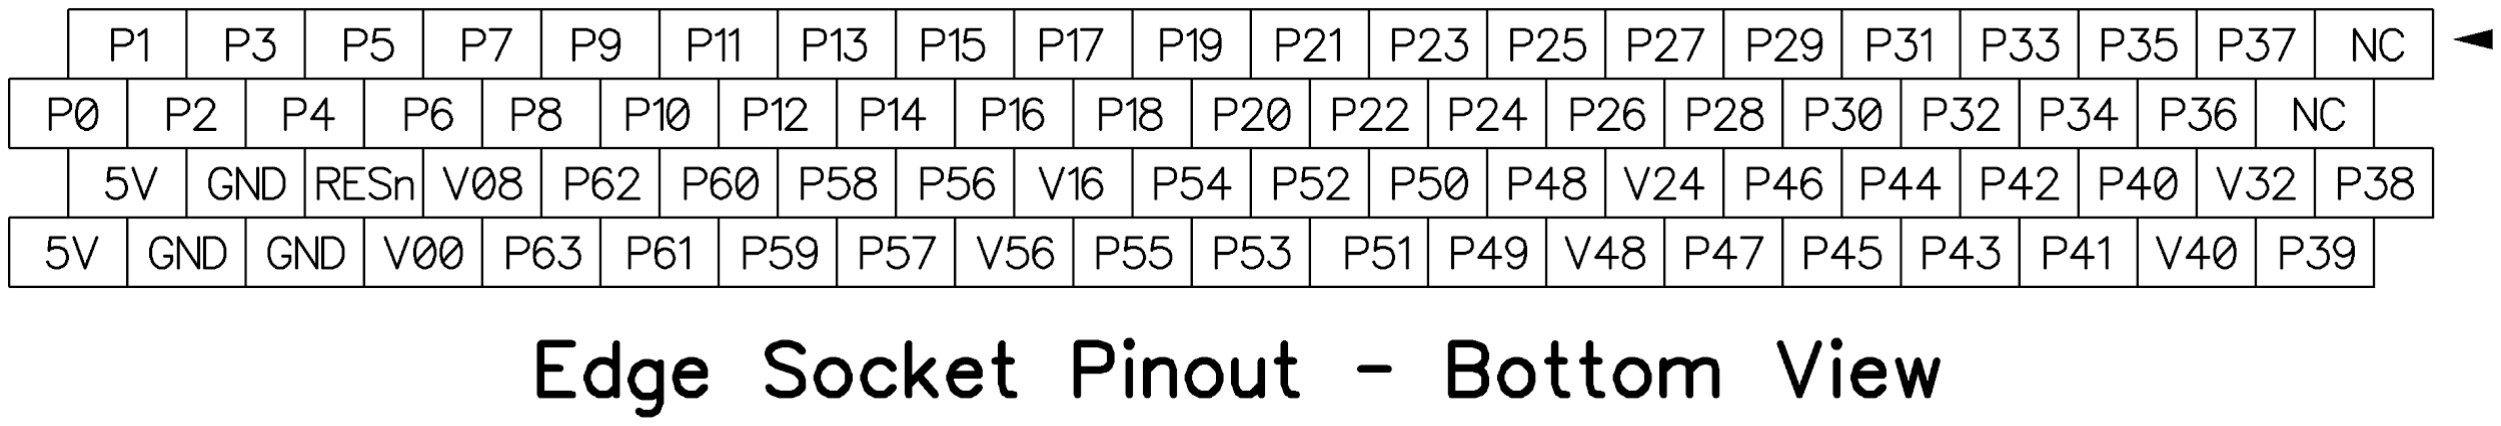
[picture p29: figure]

Copyright © Parallax Inc. | P2 Edge Breakout Board (#64029) | v1.0 03/01/2023 Page 10 of 11

### Board Dimensions

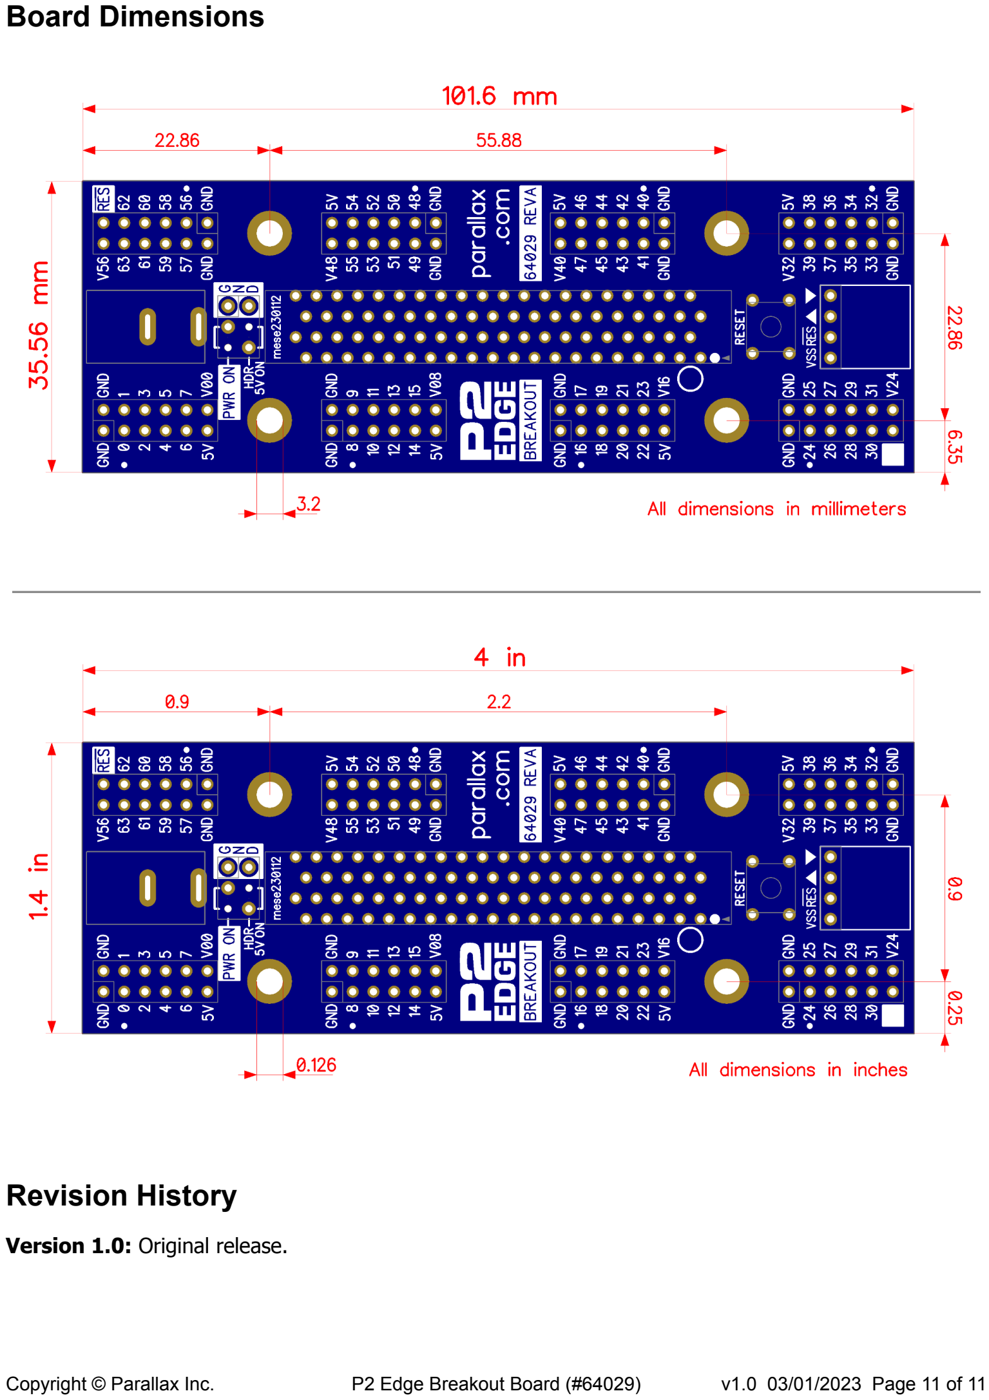
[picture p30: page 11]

### Revision History

Version 1.0: Original release.

Copyright © Parallax Inc. | P2 Edge Breakout Board (#64029) | v1.0 03/01/2023 Page 11 of 11

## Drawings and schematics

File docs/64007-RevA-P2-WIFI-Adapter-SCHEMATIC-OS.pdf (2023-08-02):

## P2 WX WiFi Adapter

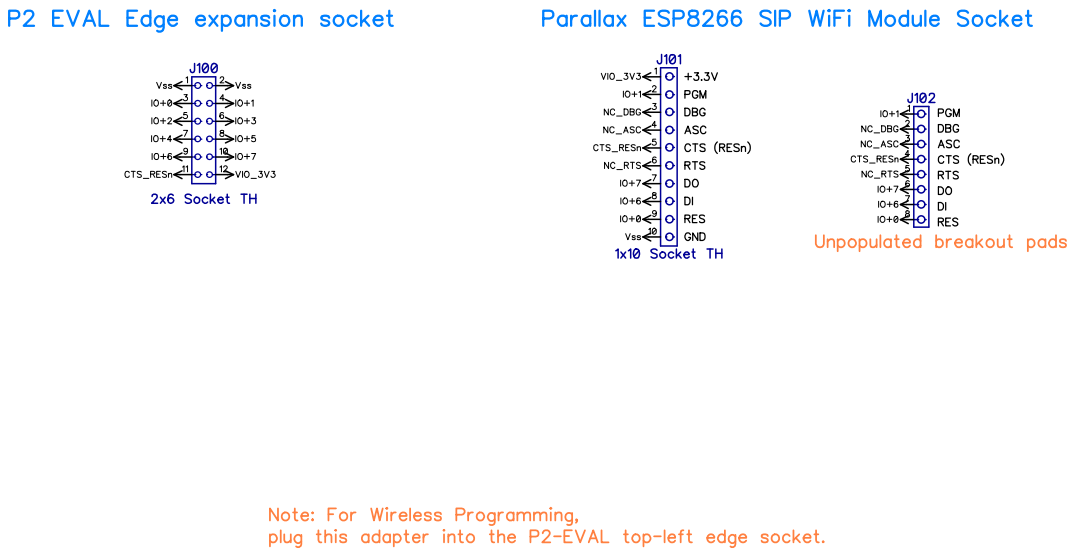
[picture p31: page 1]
P2 WX WiFi Adapter; Part Number: 64007; Revision: A; Parallax Inc. 599 Menlo Drive Rocklin, CA 95765

Copyright 2020 Parallax Incorporated. All Rights Reserved.
This is Open Source Hardware. This work is licensed under a Creative Commons
Attribution-ShareAlike 4.0 International License. The full text of the license is
available from: http://creativecommons.org/licenses/by-sa/4.0

http://www.parallax.com/

Last Update: 10 Aug 2020 (MM)

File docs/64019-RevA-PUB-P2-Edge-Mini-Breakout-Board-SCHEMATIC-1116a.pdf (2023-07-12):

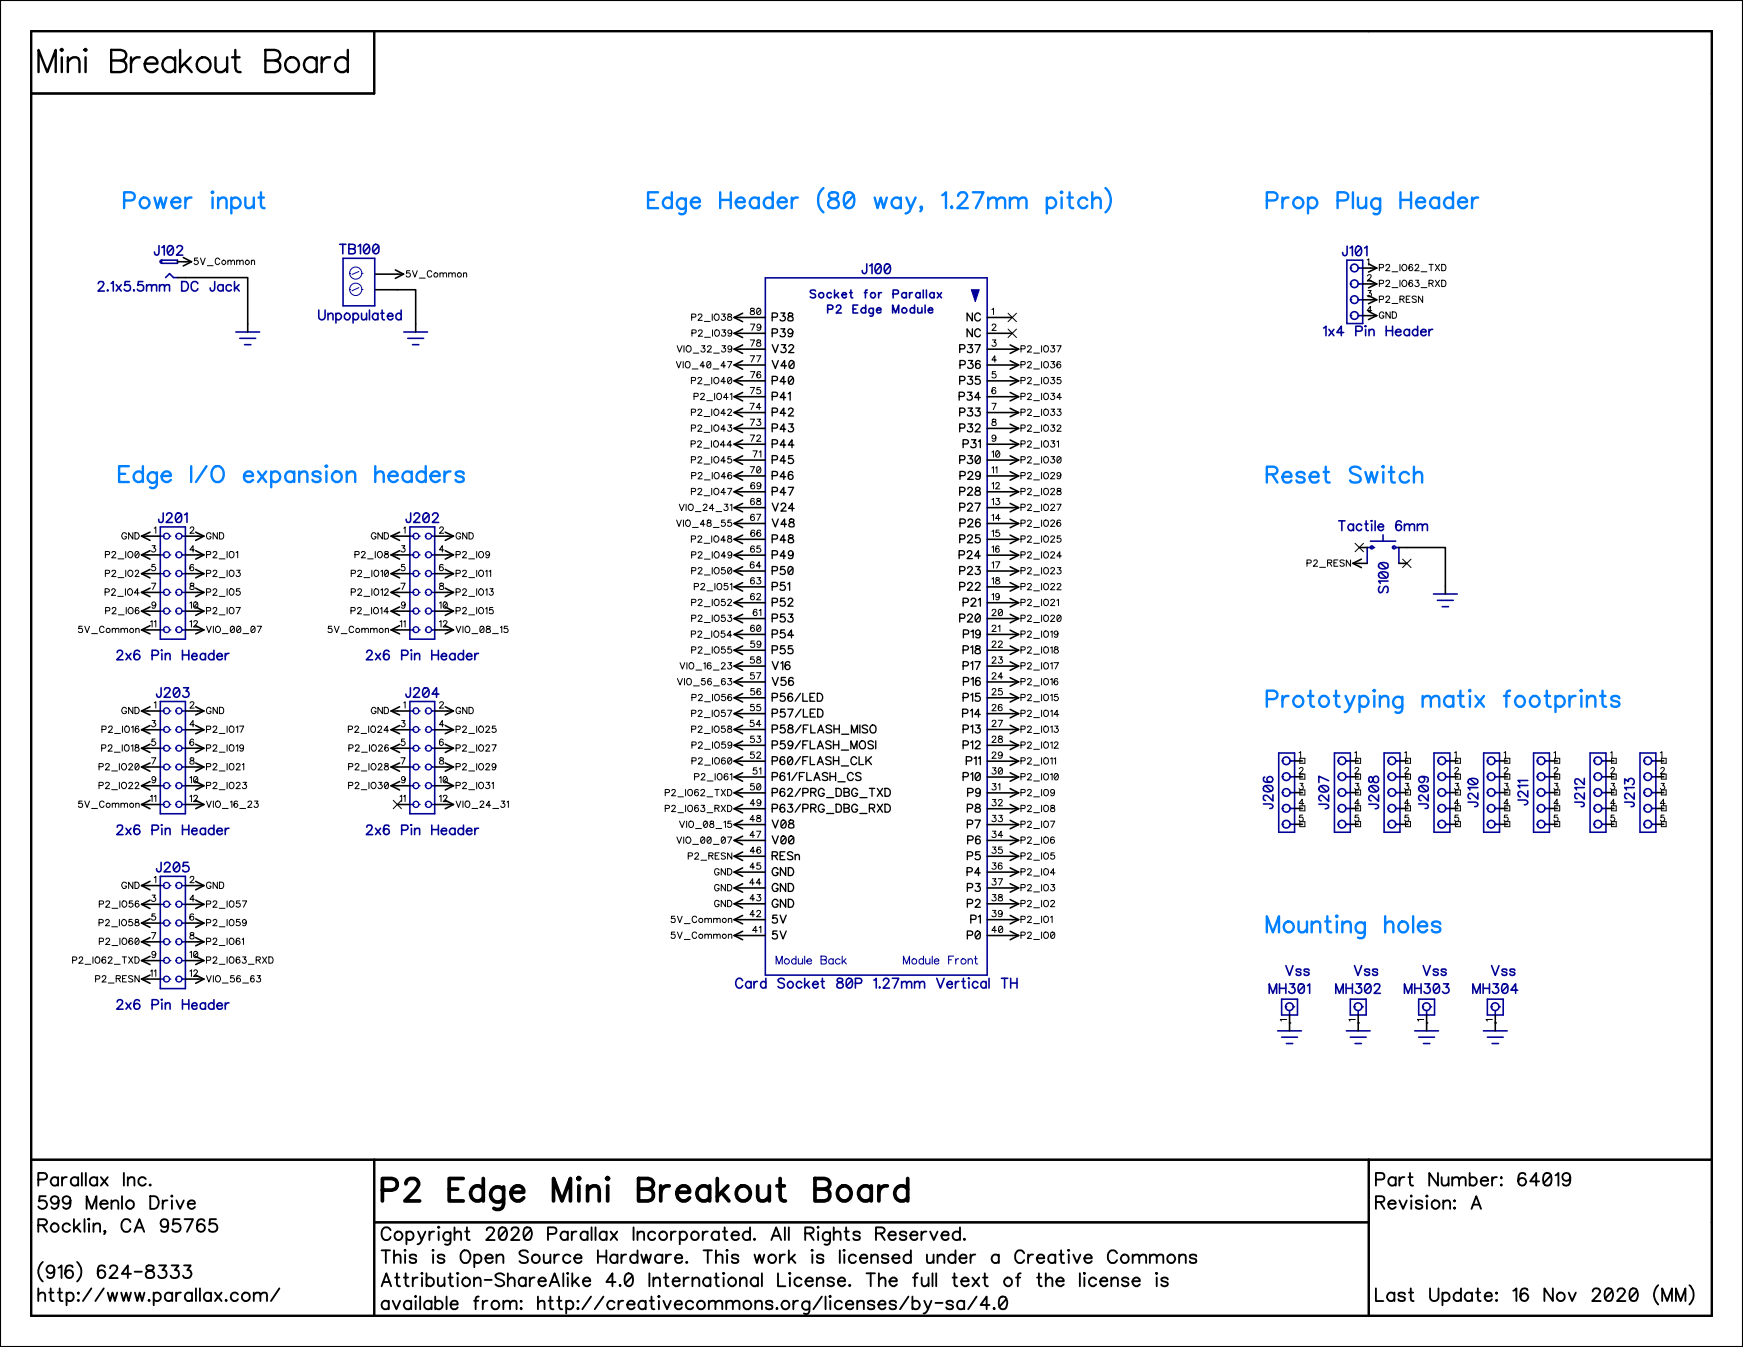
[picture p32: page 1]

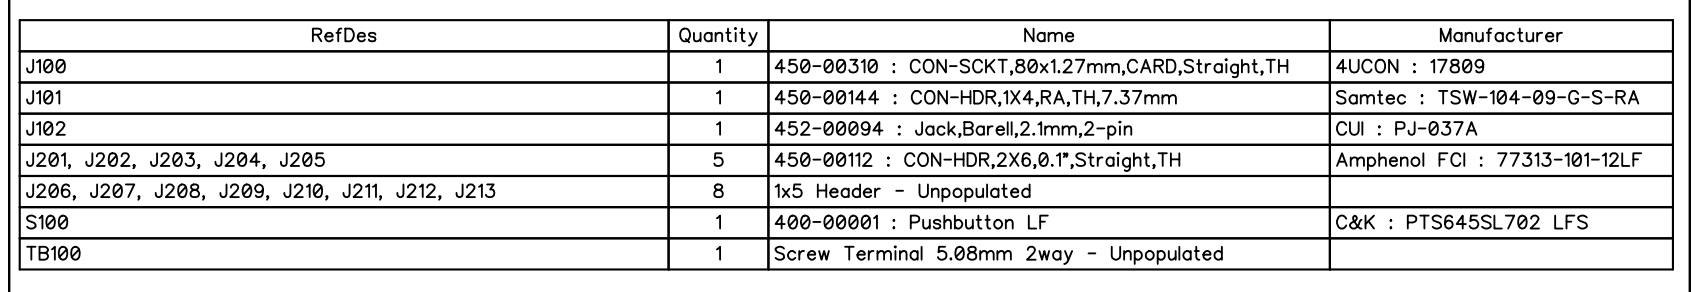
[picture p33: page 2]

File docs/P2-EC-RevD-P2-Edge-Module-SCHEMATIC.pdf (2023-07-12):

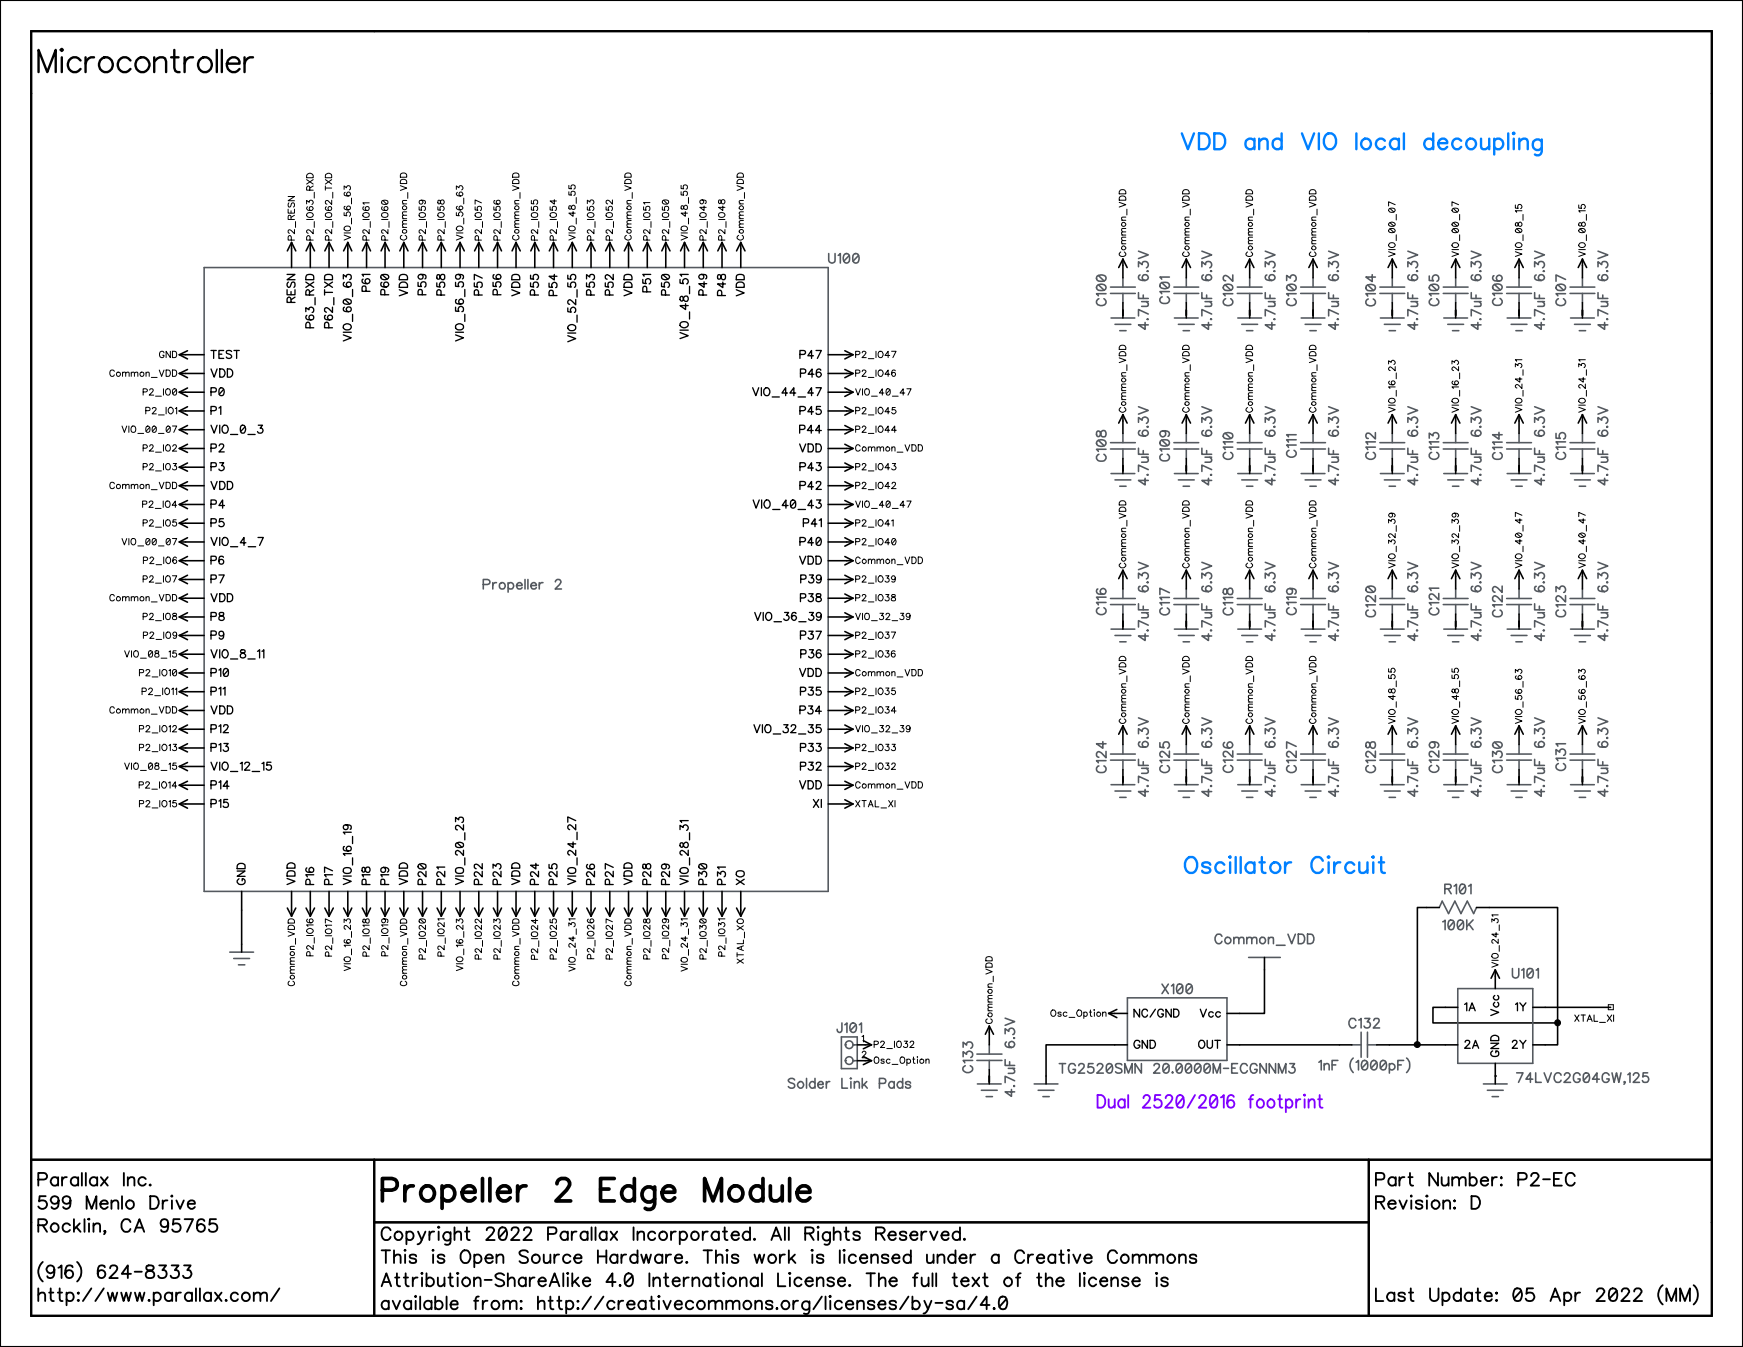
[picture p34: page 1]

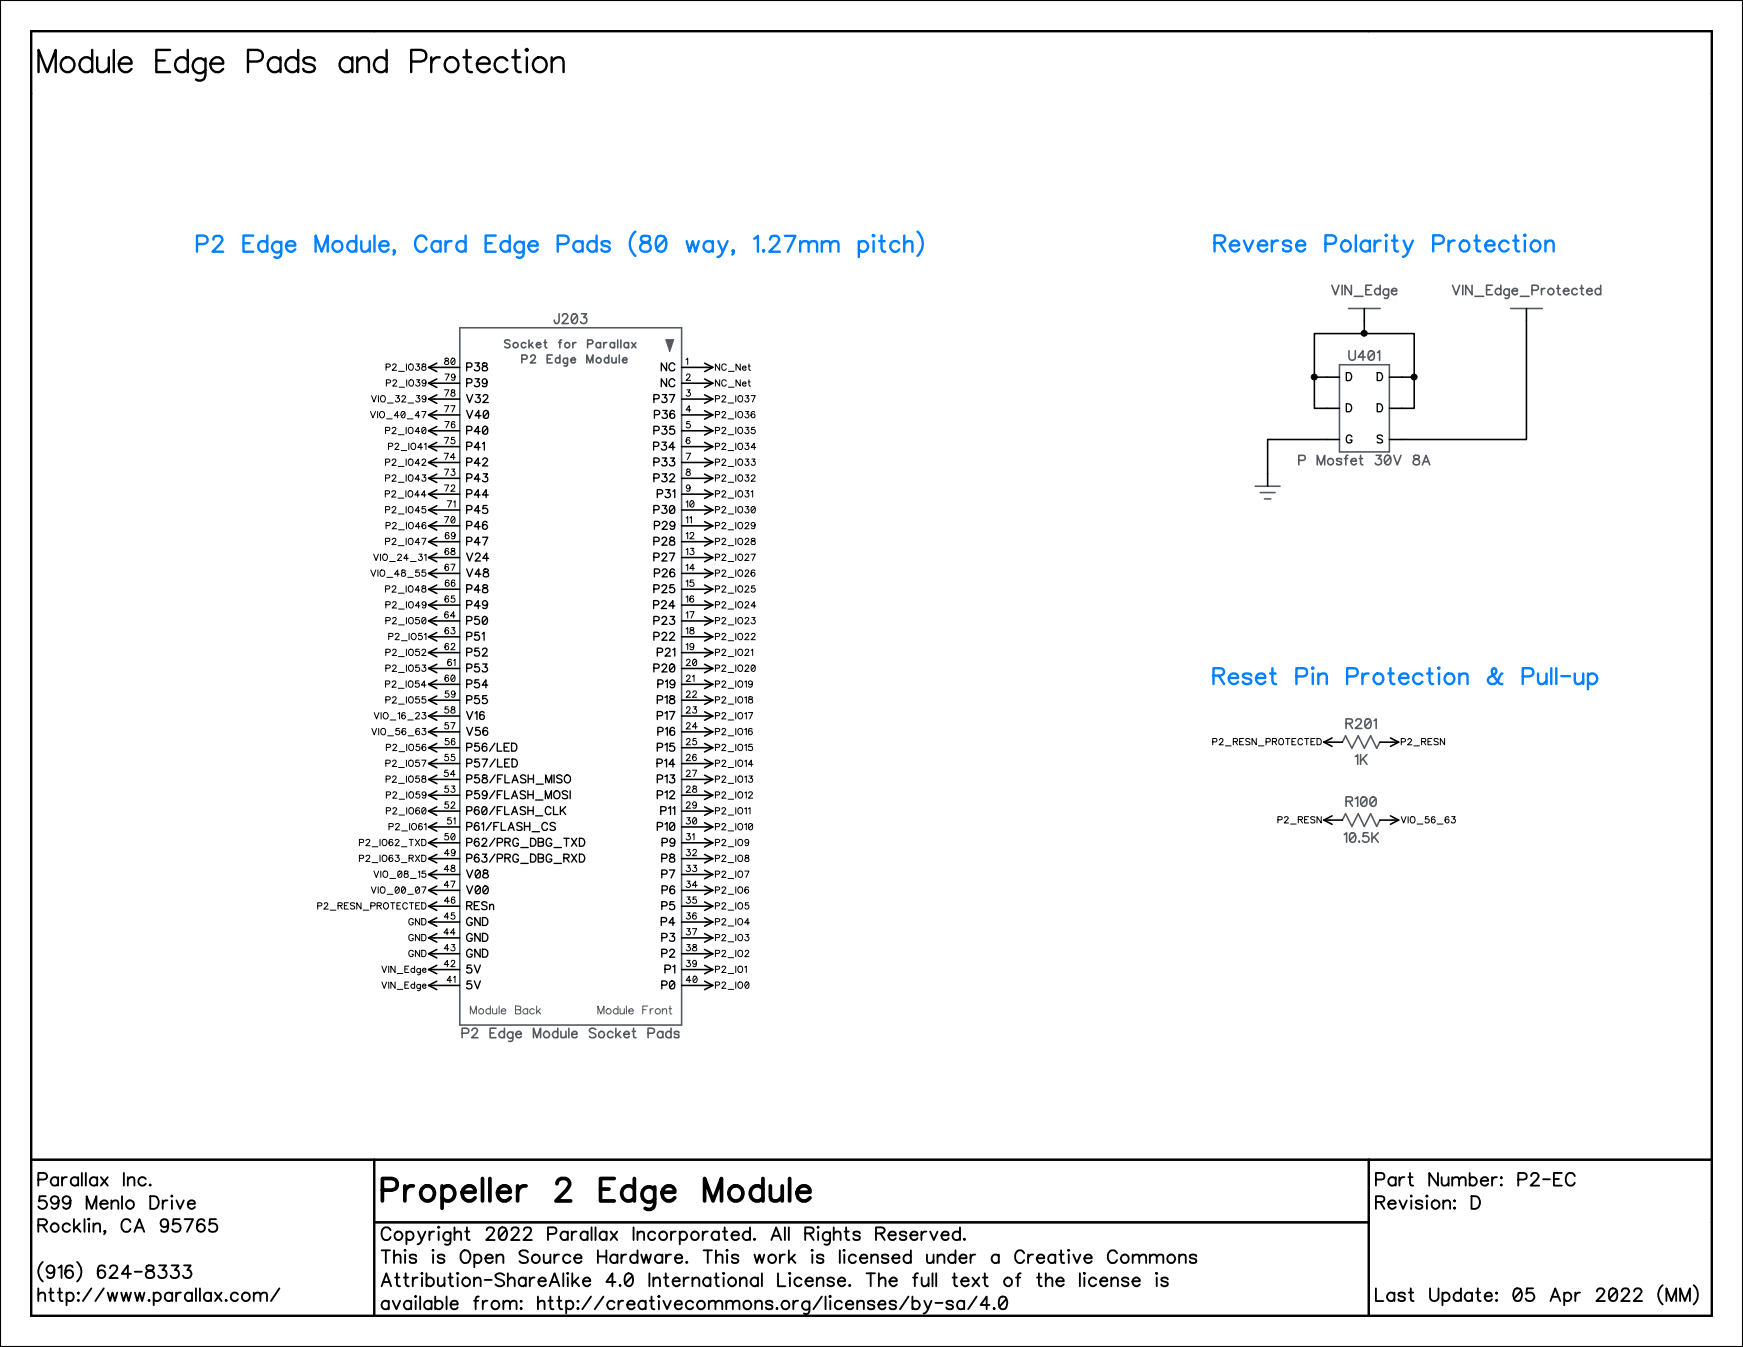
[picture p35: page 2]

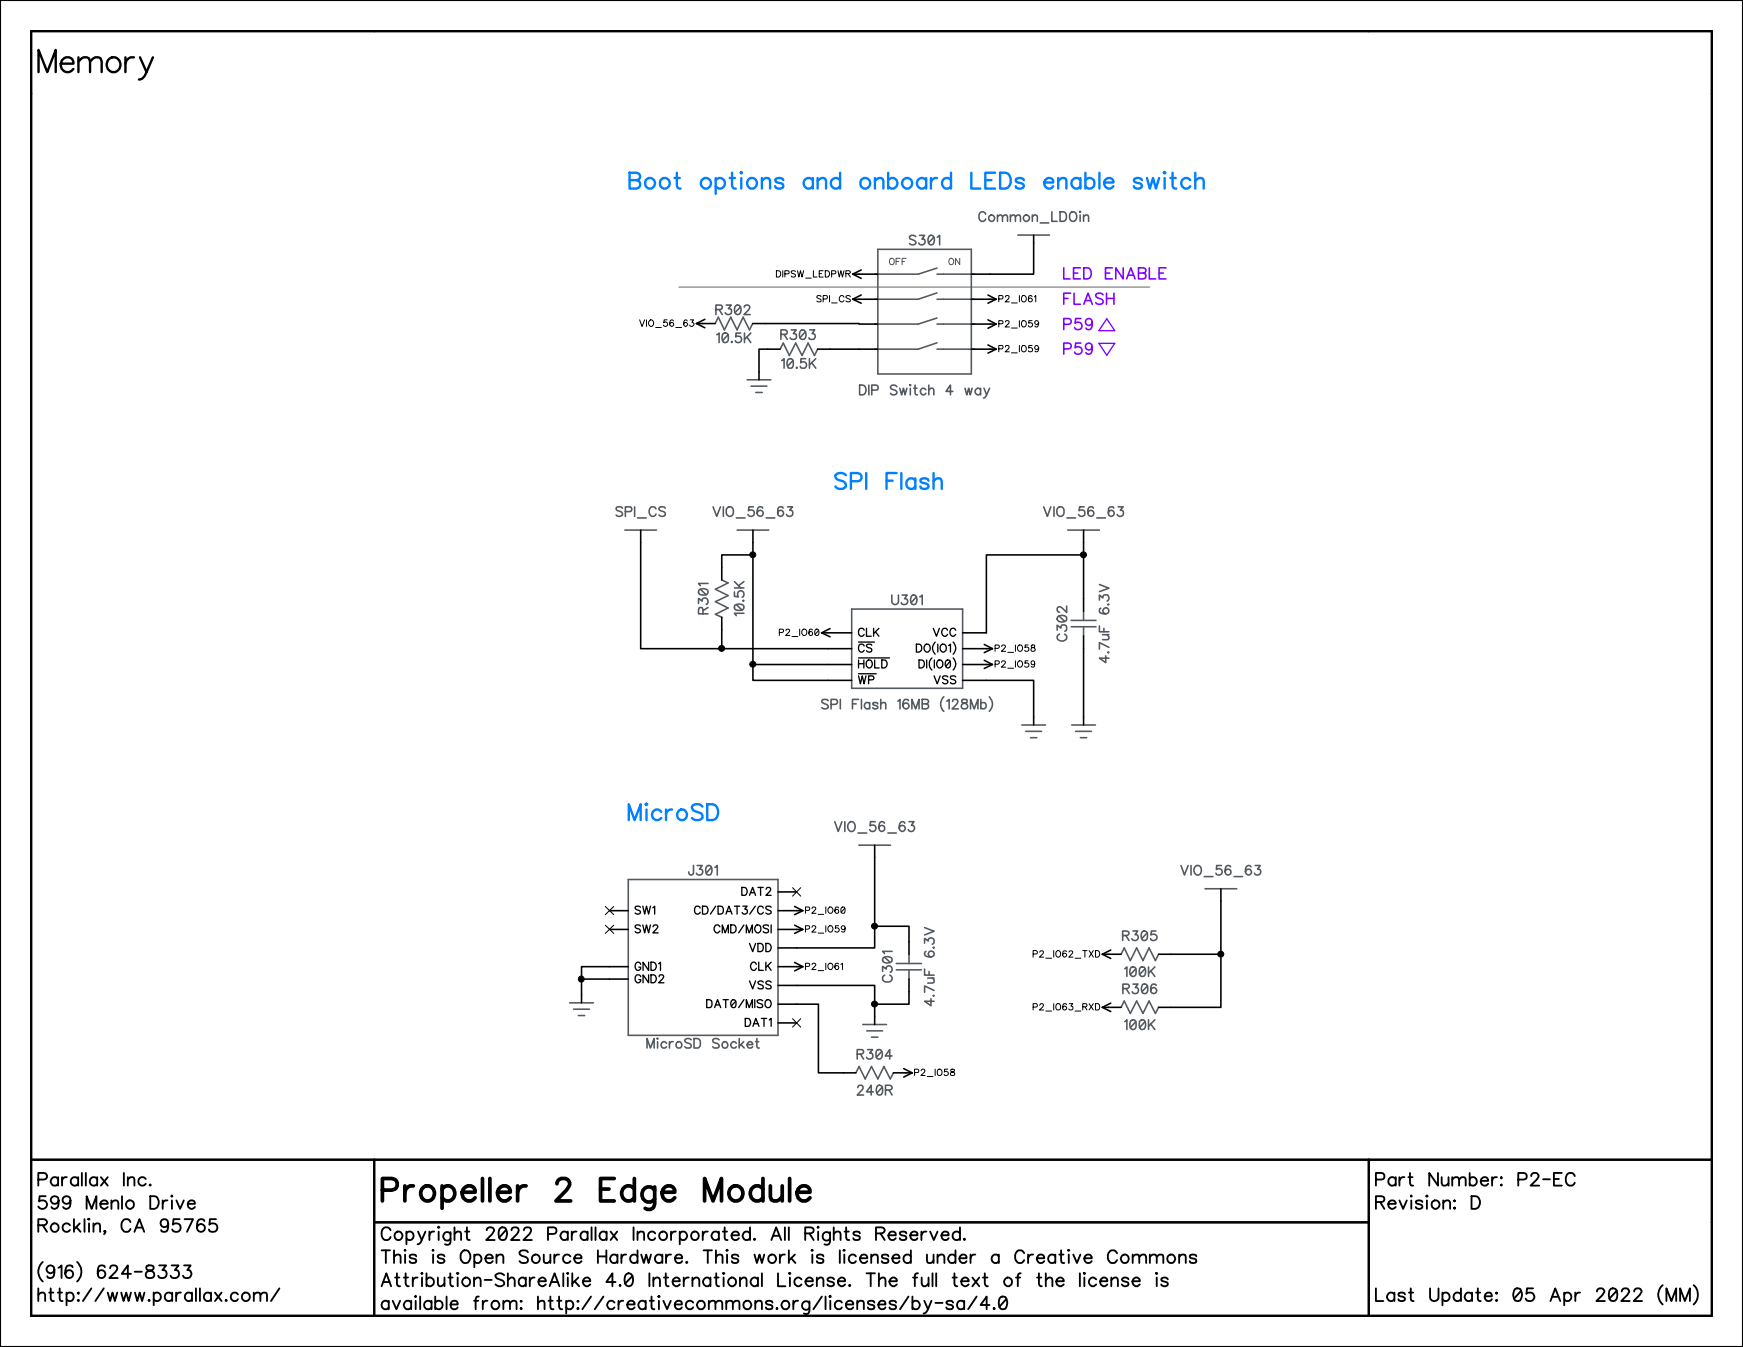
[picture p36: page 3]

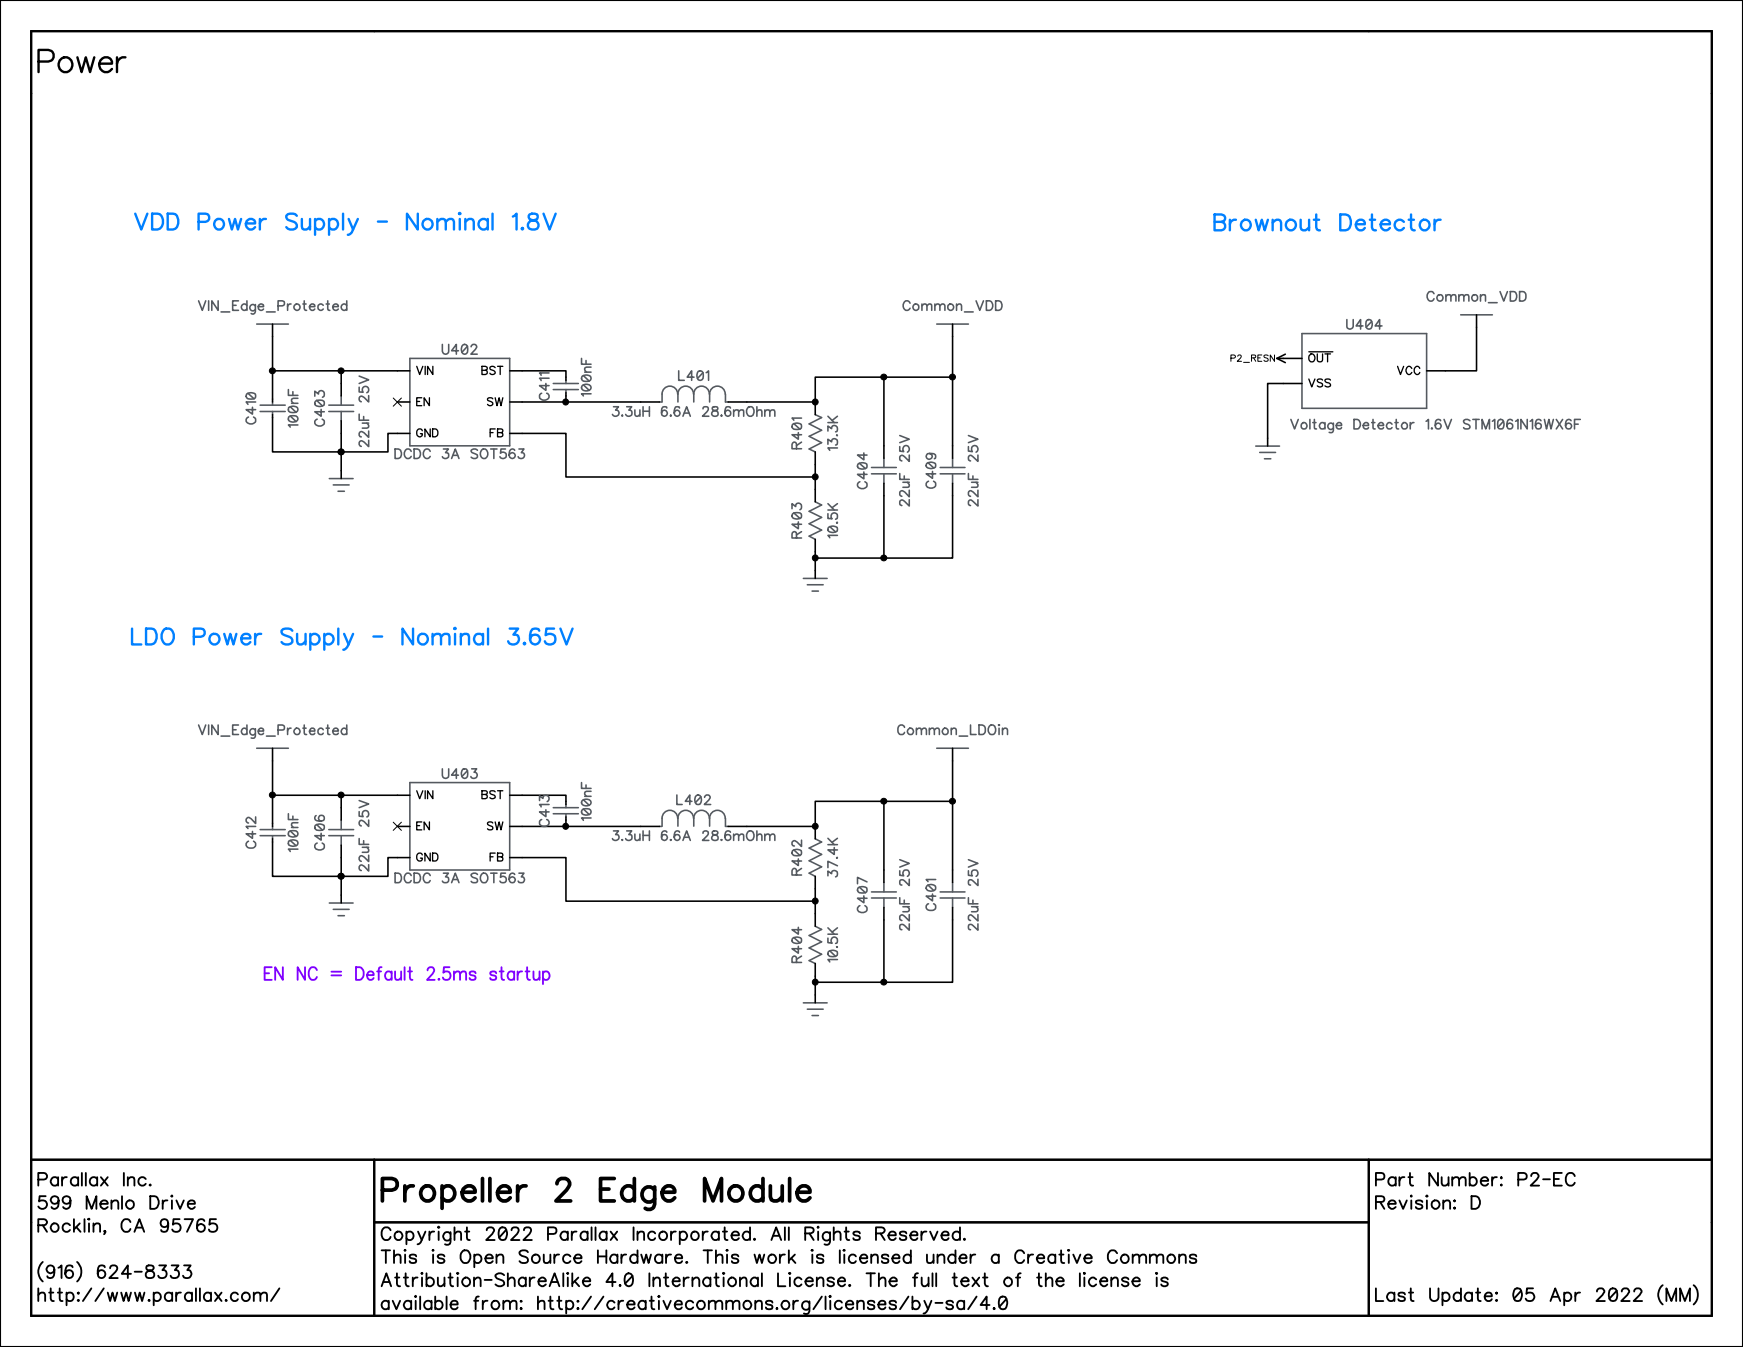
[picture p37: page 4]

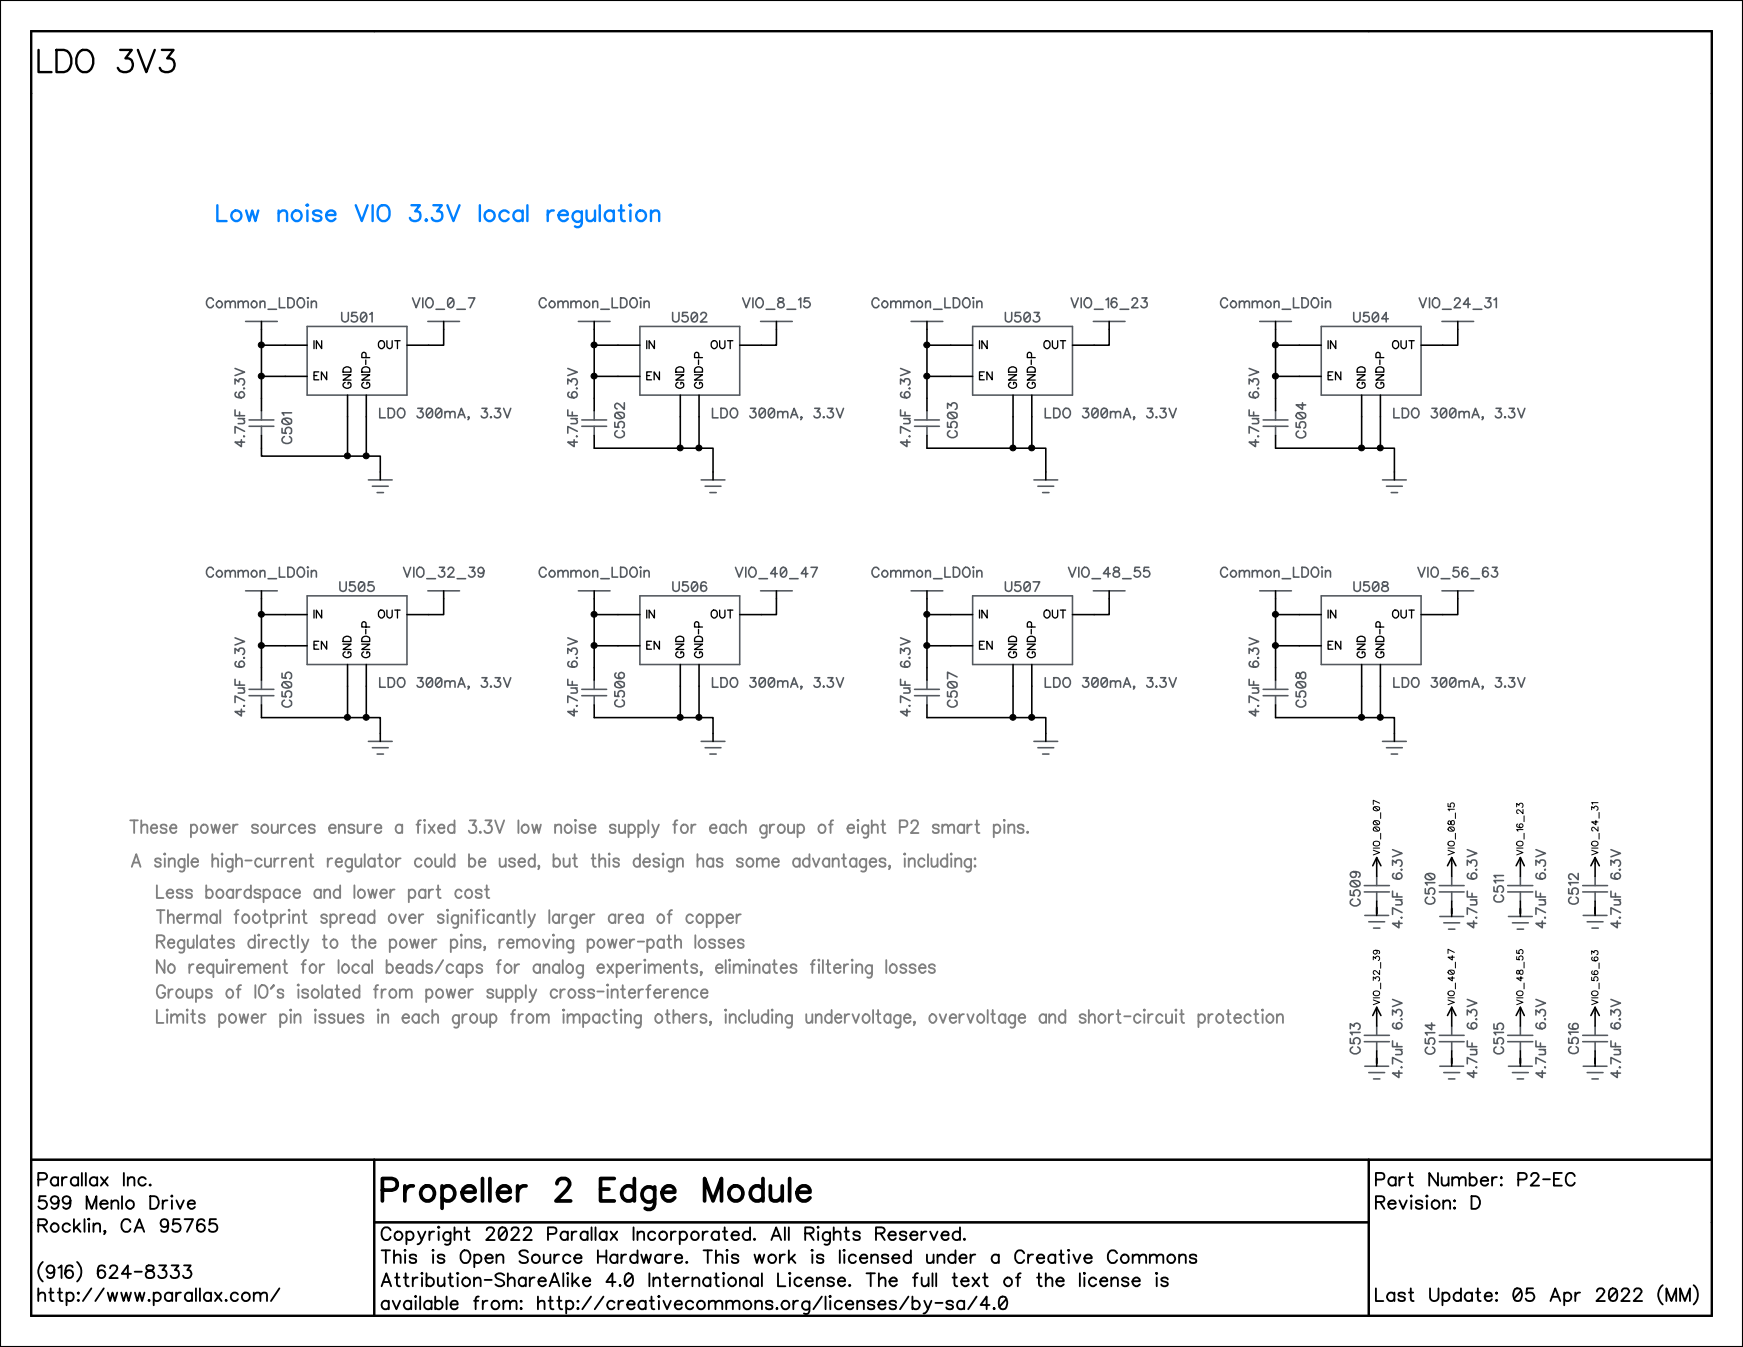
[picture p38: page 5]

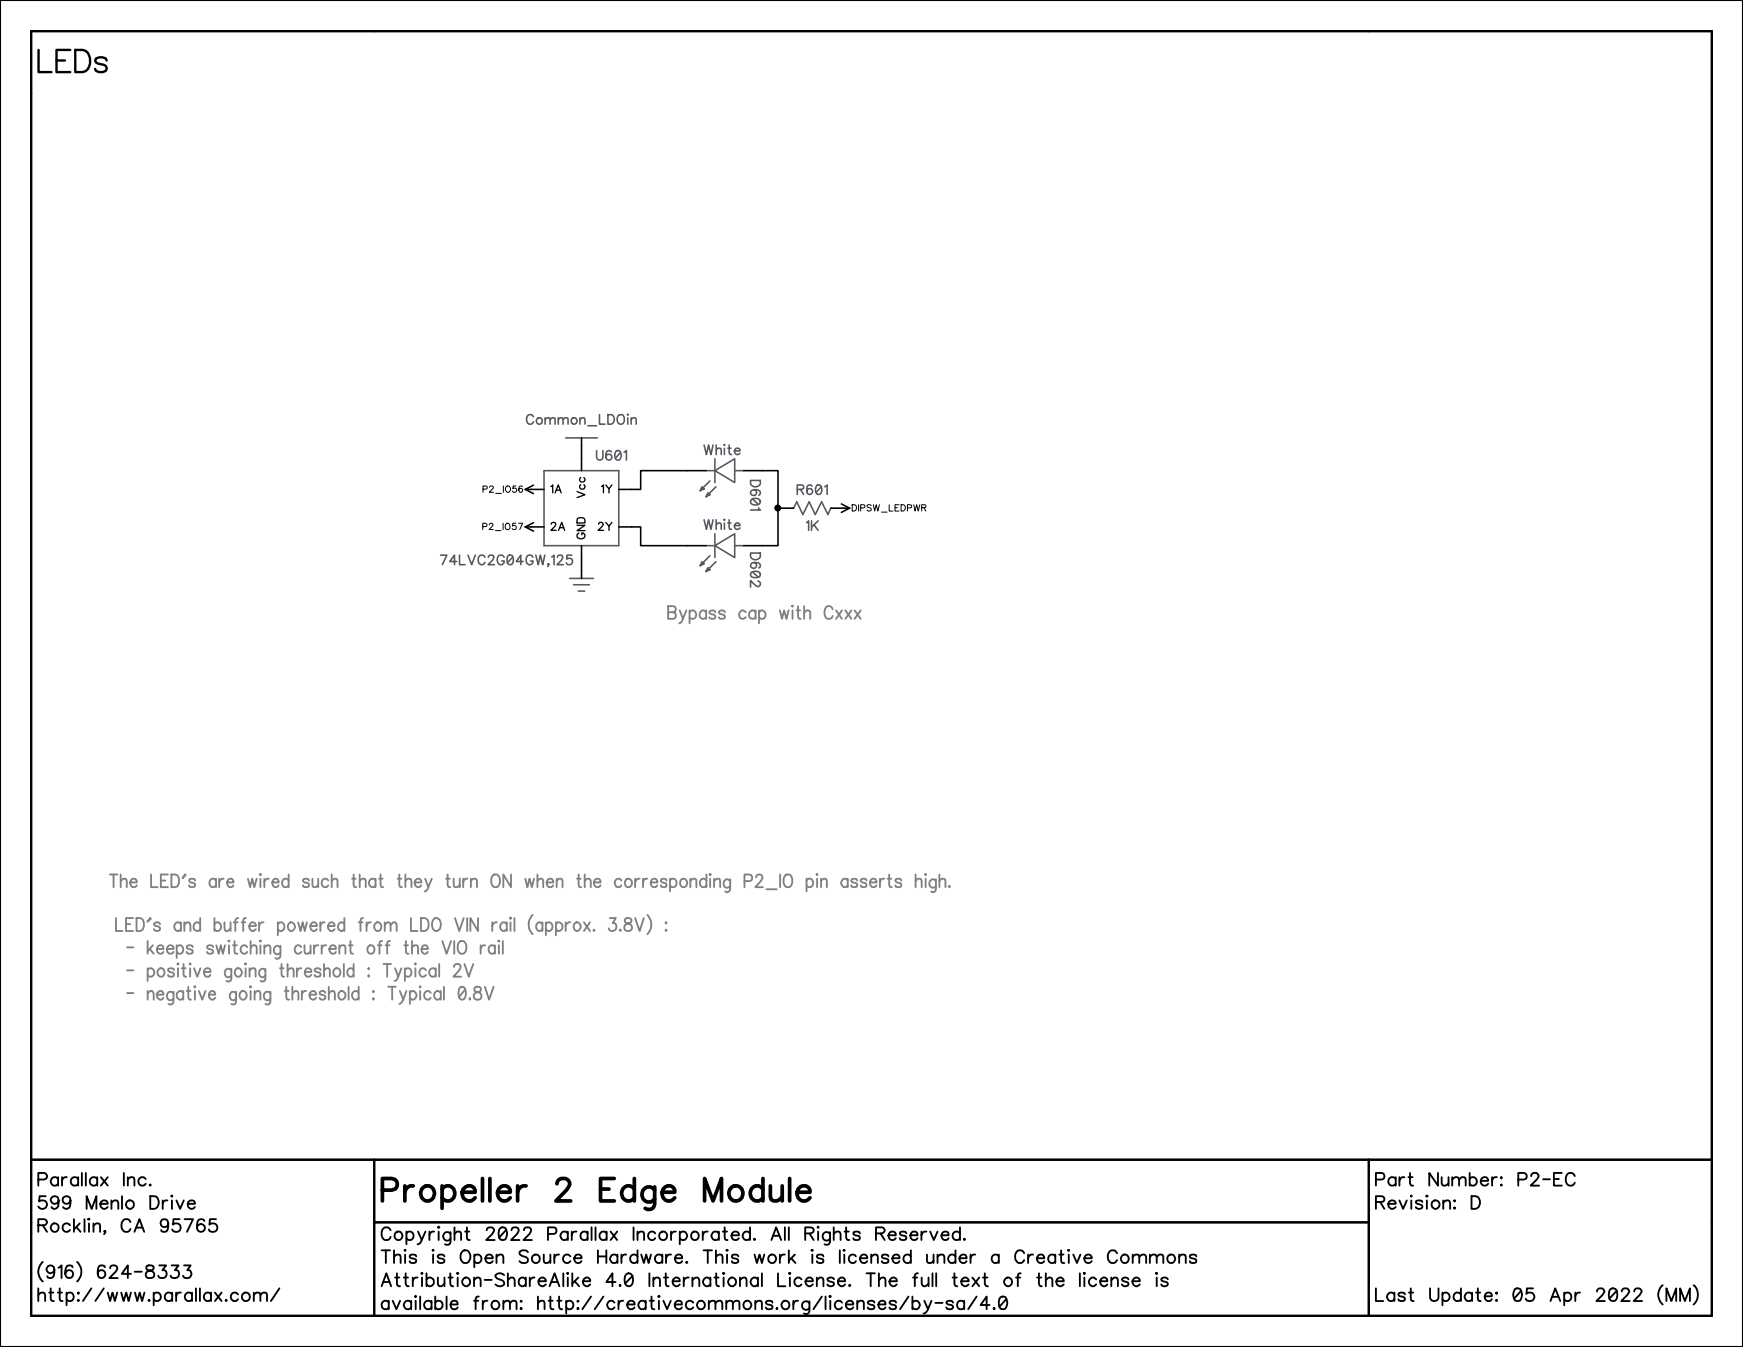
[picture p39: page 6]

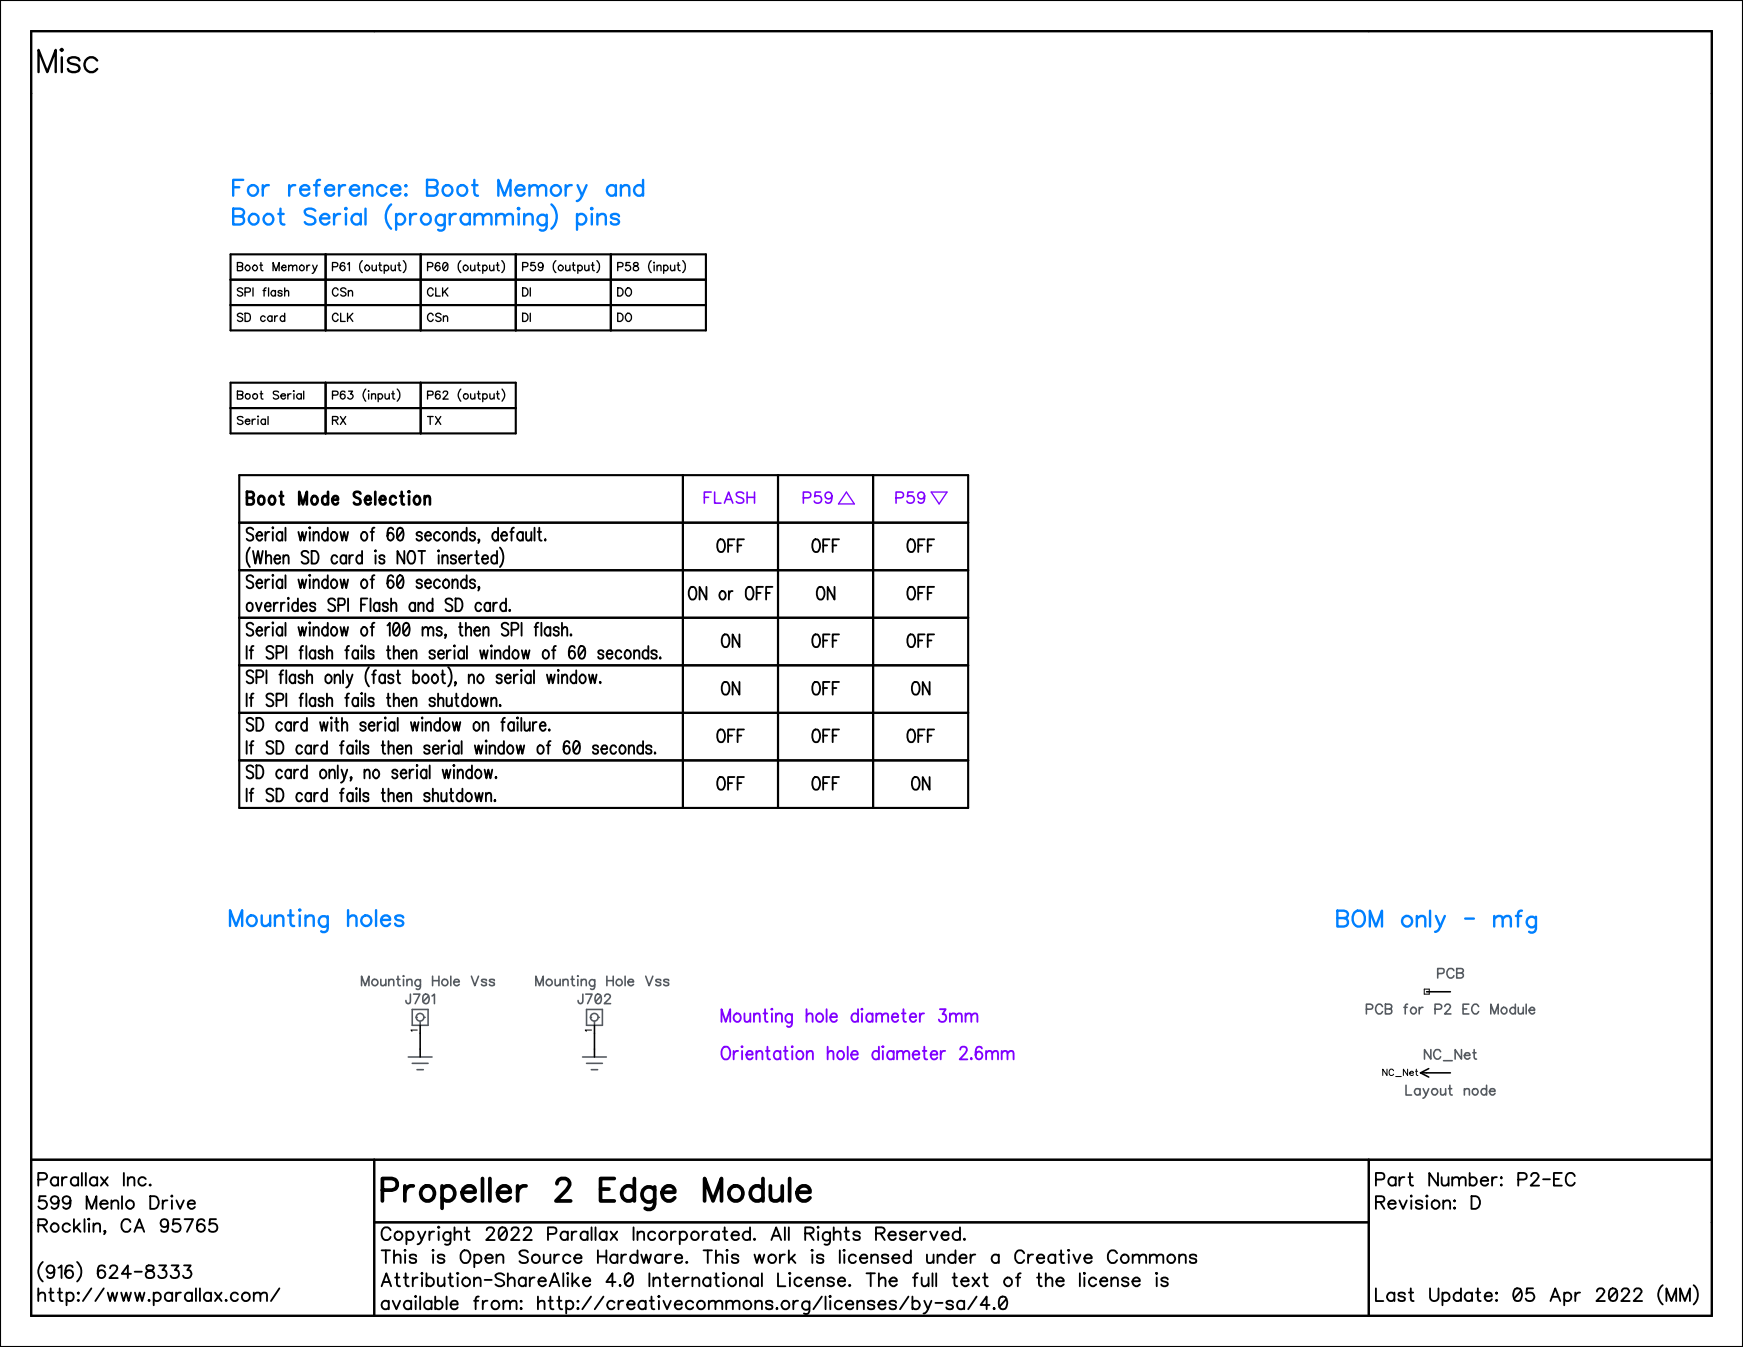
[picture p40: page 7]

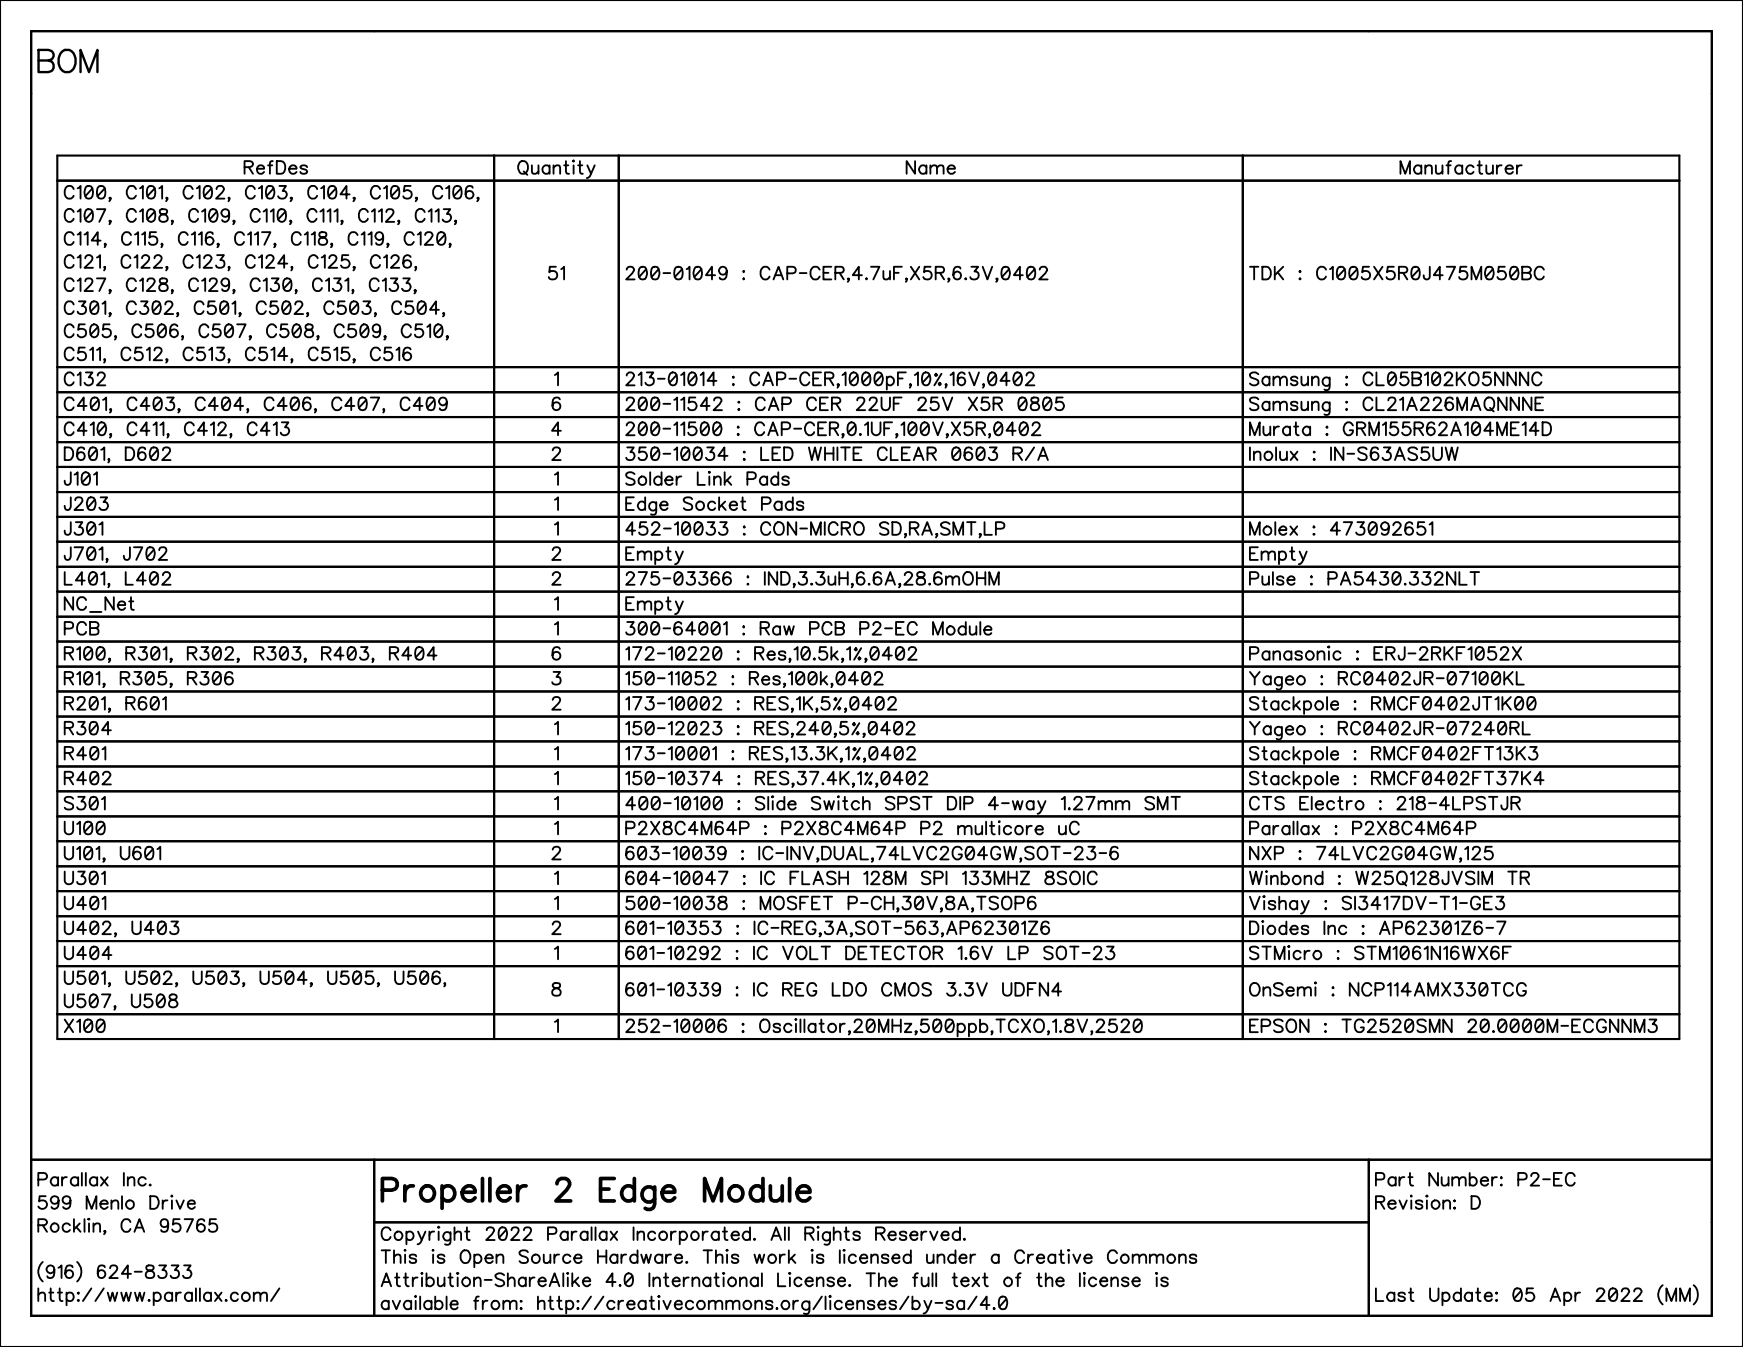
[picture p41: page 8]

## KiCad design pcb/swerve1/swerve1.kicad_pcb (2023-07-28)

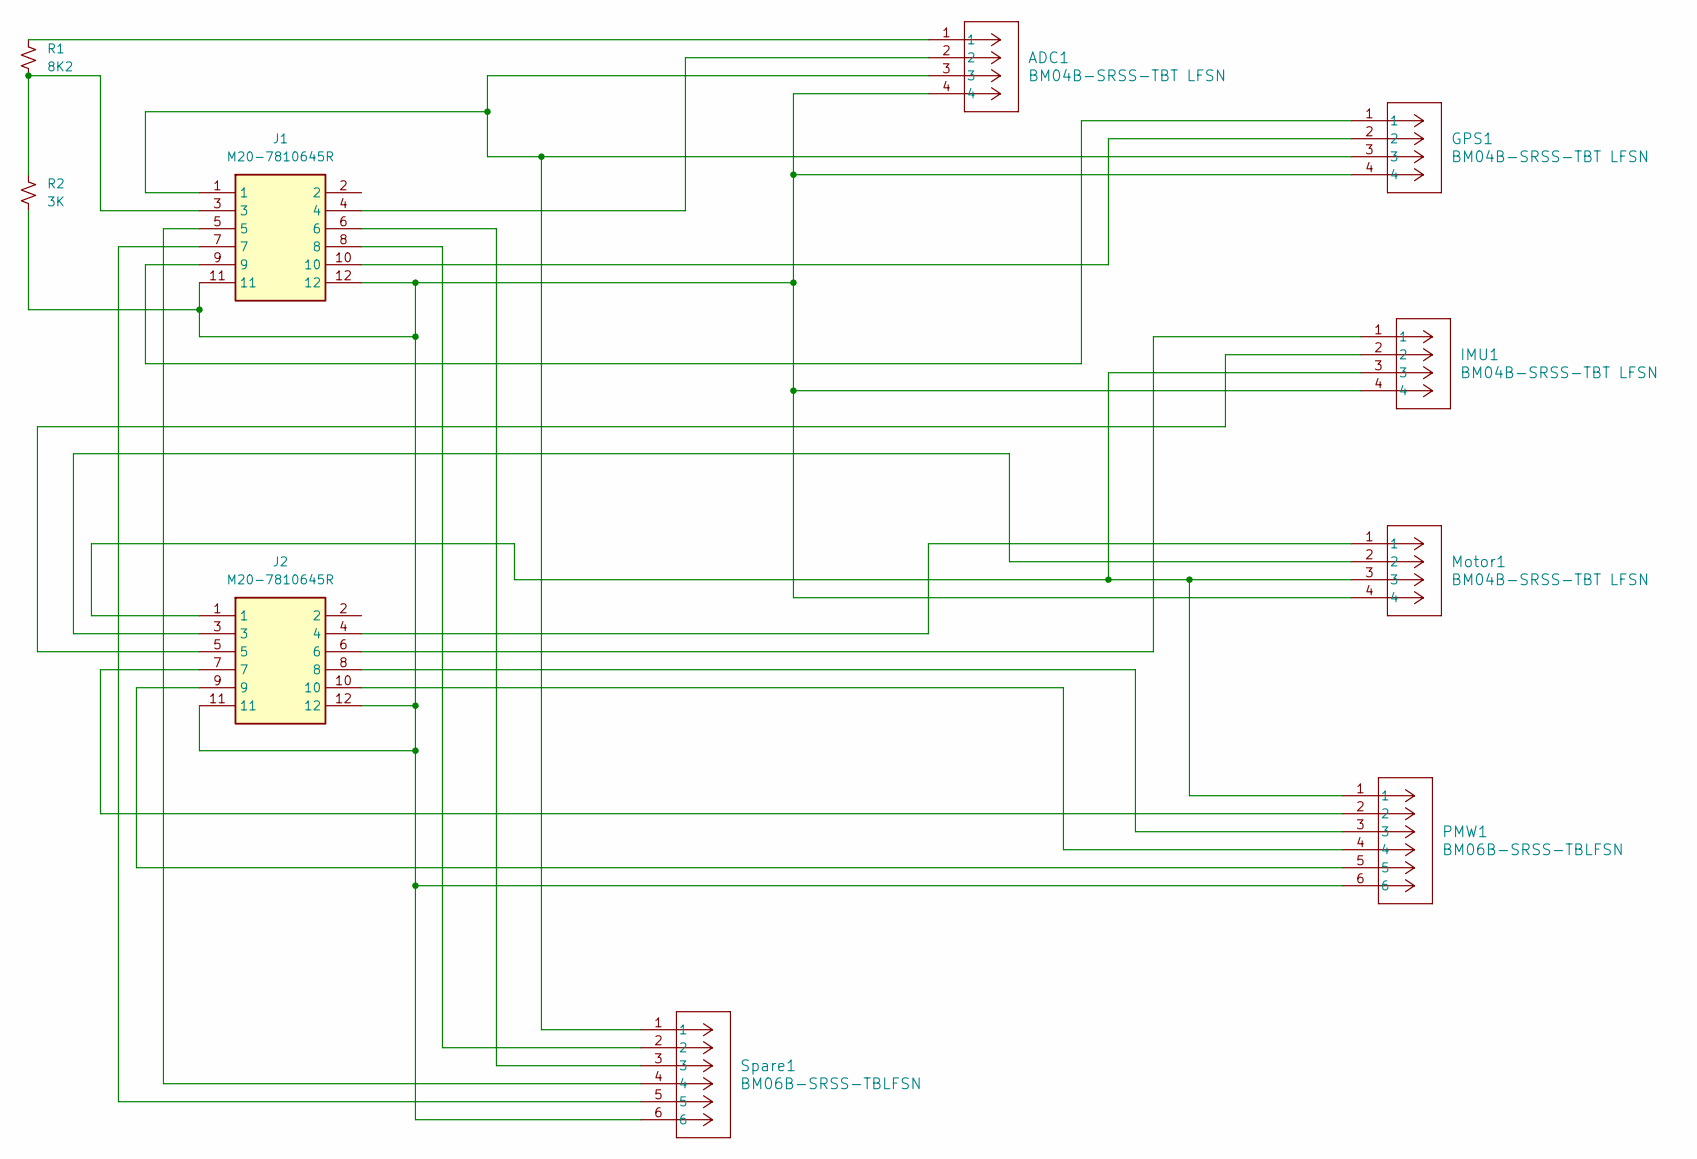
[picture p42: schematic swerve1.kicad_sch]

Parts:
ADC1: BM04B-SRSS-TBT LFSN; CONN_BM04B-SRSS-TBT LFSN_JST
GPS1: BM04B-SRSS-TBT LFSN; CONN_BM04B-SRSS-TBT LFSN_JST
IMU1: BM04B-SRSS-TBT LFSN; CONN_BM04B-SRSS-TBT LFSN_JST
J1, J2: M20-7810645R; M207810645R; Manufacturer_Part_Number M20-7810645R; Mouser Part Number 855-M20-7810645R
Motor1: BM04B-SRSS-TBT LFSN; CONN_BM04B-SRSS-TBT LFSN_JST
PMW1: BM06B-SRSS-TBLFSN; CONN_BM06B-SRSS-TB_JST
R1: 8K2; R_0805_2012Metric_Pad1.20x1.40mm_HandSolder
R2: 3K; R_0805_2012Metric_Pad1.20x1.40mm_HandSolder
Spare1: BM06B-SRSS-TBLFSN; CONN_BM06B-SRSS-TB_JST

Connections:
unnamed: ADC1.1, R1.1
unnamed: ADC1.2, J1.4
unnamed: ADC1.3, GPS1.3, J1.1, Spare1.1
unnamed: ADC1.4, GPS1.4, IMU1.4, J1.11, J1.12, J2.11, J2.12, Motor1.4, PMW1.6, R2.2, Spare1.6
unnamed: GPS1.1, J1.9
unnamed: GPS1.2, J1.10
unnamed: IMU1.1, J2.6
unnamed: IMU1.2, J2.5
unnamed: IMU1.3, J2.1, Motor1.3, PMW1.1
unnamed: J1.3, R1.2, R2.1
unnamed: J1.5, Spare1.4
unnamed: J1.6, Spare1.3
unnamed: J1.7, Spare1.5
unnamed: J1.8, Spare1.2
unnamed: J2.3, Motor1.2
unnamed: J2.4, Motor1.1
unnamed: J2.7, PMW1.2
unnamed: J2.8, PMW1.3
unnamed: J2.9, PMW1.5
unnamed: J2.10, PMW1.4

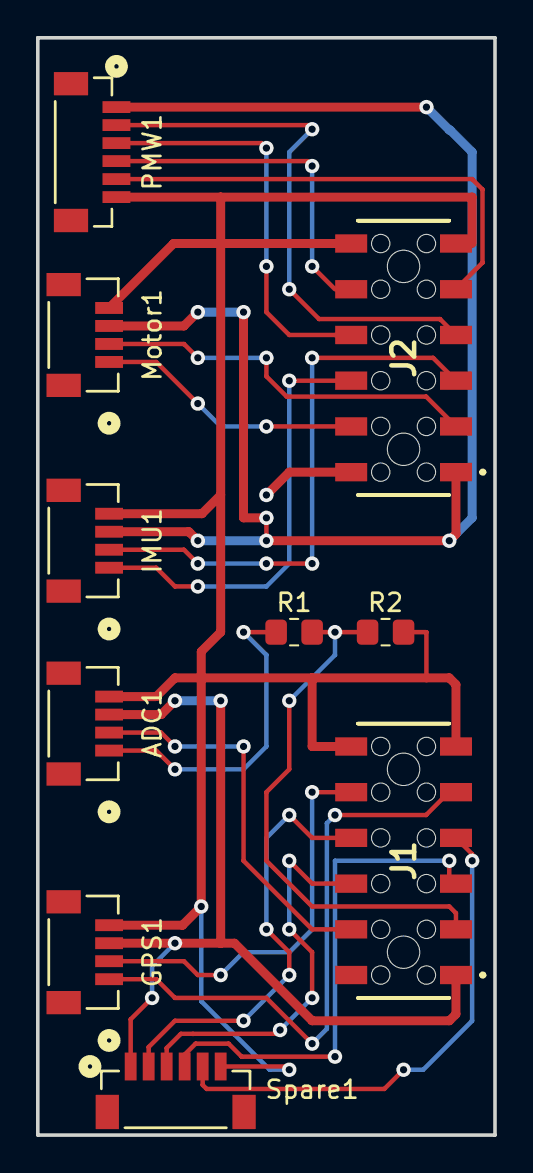
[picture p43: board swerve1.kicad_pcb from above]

Board: 2 copper layers, 25.4 x 61.0 mm, 10 parts (0 on the bottom side), 20 nets.

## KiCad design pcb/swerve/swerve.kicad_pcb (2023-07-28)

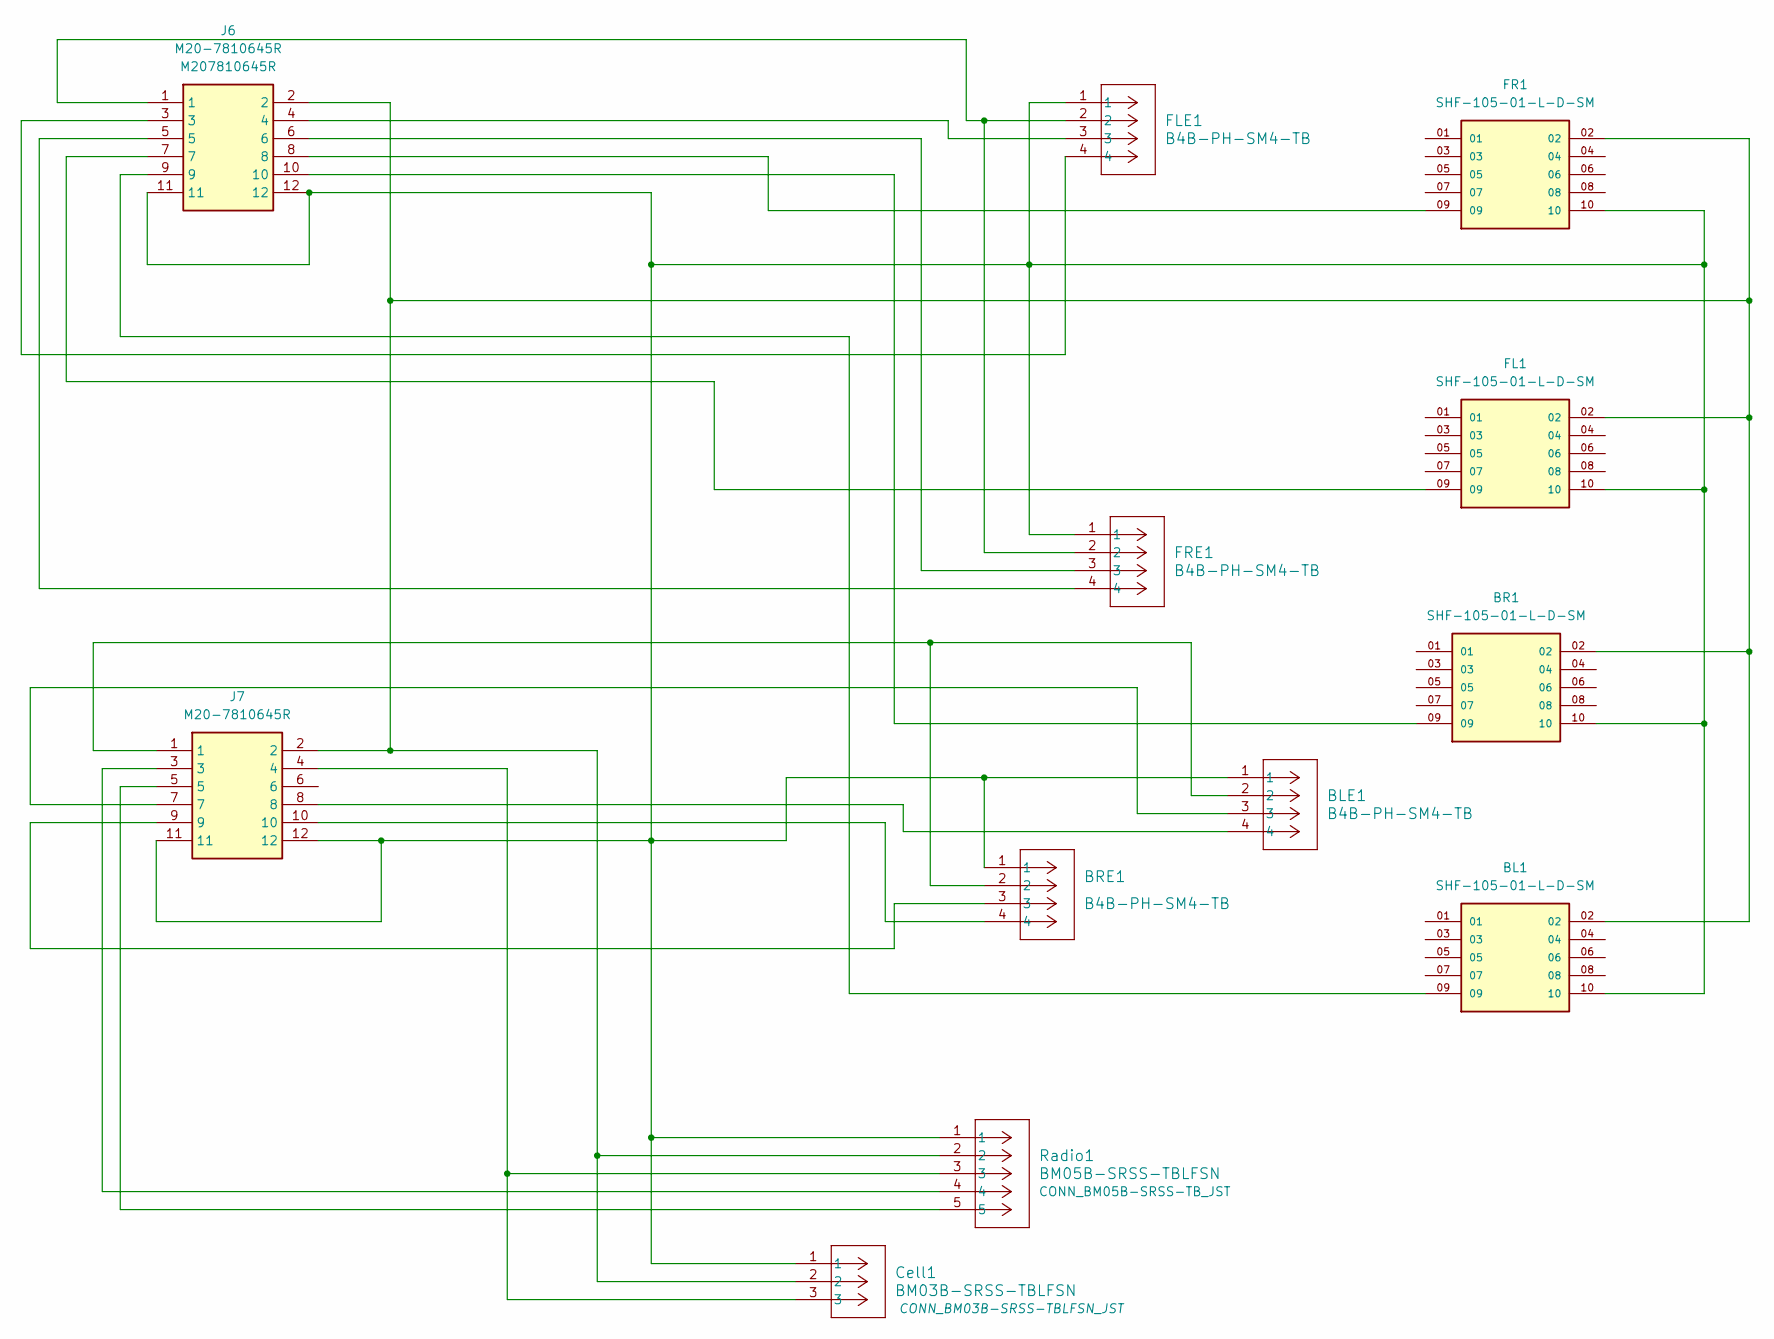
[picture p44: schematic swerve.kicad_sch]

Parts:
BL1: SHF-105-01-L-D-SM; SAMTEC_SHF-105-01-L-D-SM; PARTREV A
BLE1: B4B-PH-SM4-TB; JST_PH_B4B-PH-SM4-TB_1x04-1MP_P2.00mm_Vertical
BR1: SHF-105-01-L-D-SM; SAMTEC_SHF-105-01-L-D-SM; PARTREV A
BRE1: B4B-PH-SM4-TB; JST_PH_B4B-PH-SM4-TB_1x04-1MP_P2.00mm_Vertical
Cell1: BM03B-SRSS-TBLFSN; CONN_BM03B-SRSS-TBLFSN_JST
FL1: SHF-105-01-L-D-SM; SAMTEC_SHF-105-01-L-D-SM; PARTREV A
FLE1: B4B-PH-SM4-TB; JST_PH_B4B-PH-SM4-TB_1x04-1MP_P2.00mm_Vertical
FR1: SHF-105-01-L-D-SM; SAMTEC_SHF-105-01-L-D-SM; PARTREV A
FRE1: B4B-PH-SM4-TB; JST_PH_B4B-PH-SM4-TB_1x04-1MP_P2.00mm_Vertical
J6, J7: M20-7810645R; M207810645R; Manufacturer_Part_Number M20-7810645R; Mouser Part Number 855-M20-7810645R
Radio1: BM05B-SRSS-TBLFSN; CONN_BM05B-SRSS-TB_JST

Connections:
unnamed: BL1.02, BR1.02, Cell1.2, FL1.02, FR1.02, J6.2, J7.2, Radio1.2
unnamed: BL1.09, J6.9
unnamed: BL1.10, BLE1.1, BR1.10, BRE1.1, Cell1.1, FL1.10, FLE1.1, FR1.10, FRE1.1, J6.11, J6.12, J7.11, J7.12, Radio1.1
unnamed: BLE1.2, BRE1.2, J7.1
unnamed: BLE1.3, J7.7
unnamed: BLE1.4, J7.8
unnamed: BR1.09, J6.10
unnamed: BRE1.3, J7.9
unnamed: BRE1.4, J7.10
unnamed: Cell1.3, J7.4, Radio1.3
unnamed: FL1.09, J6.7
unnamed: FLE1.2, FRE1.2, J6.1
unnamed: FLE1.3, J6.4
unnamed: FLE1.4, J6.3
unnamed: FR1.09, J6.8
unnamed: FRE1.3, J6.6
unnamed: FRE1.4, J6.5
unnamed: J7.3, Radio1.4
unnamed: J7.5, Radio1.5

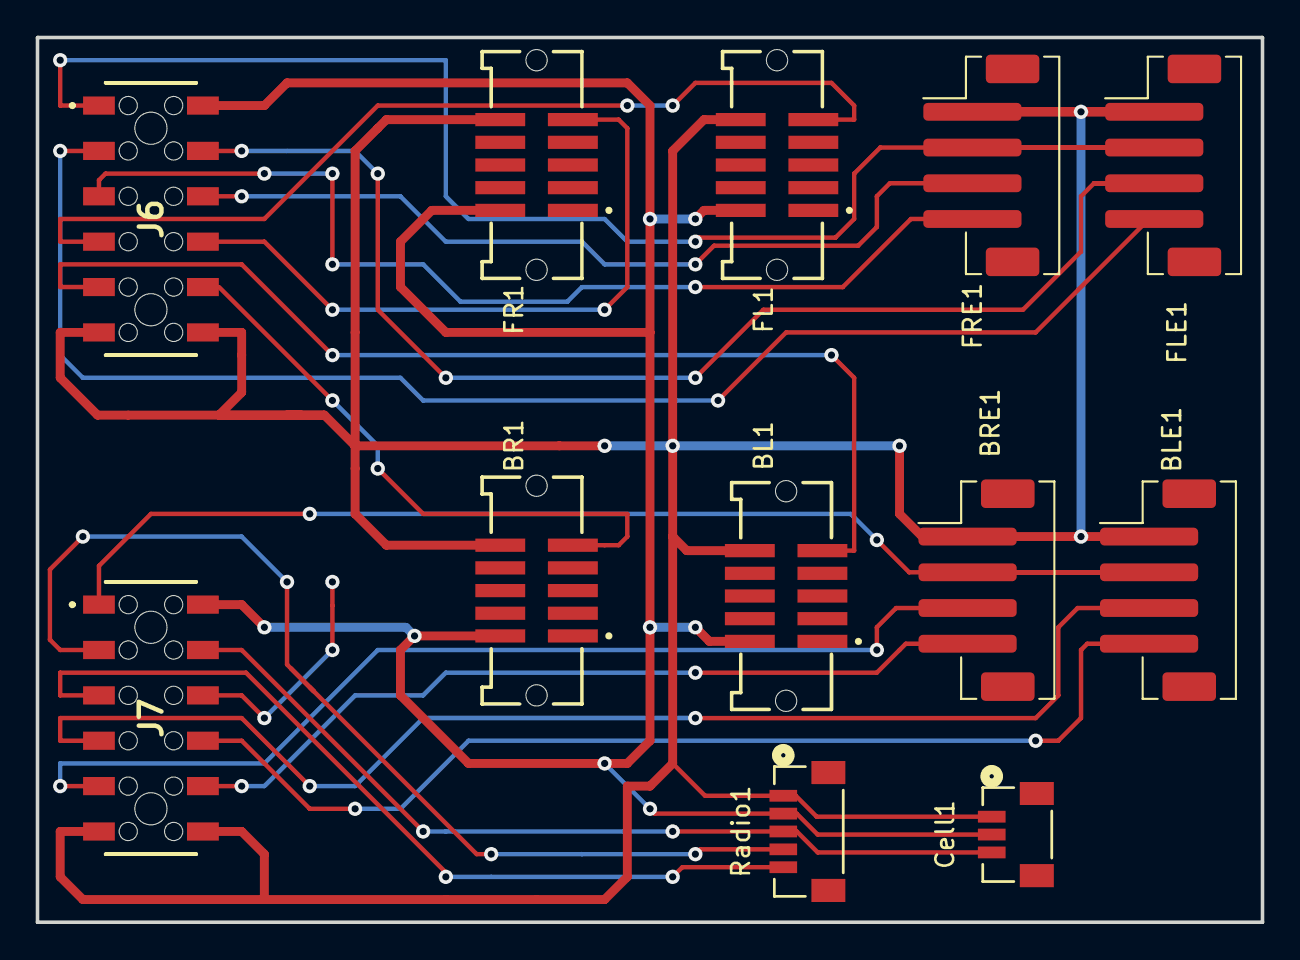
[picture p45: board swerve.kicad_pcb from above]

Board: 2 copper layers, 68.6 x 49.5 mm, 12 parts (0 on the bottom side), 19 nets.

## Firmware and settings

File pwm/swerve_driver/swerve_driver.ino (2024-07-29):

// Swerve module driver
//   https://www.adafruit.com/product/4900
// 
// Based on example by Nicholas Zambetti <http://www.zambetti.com>
// pwm servo out on pins 29, 28 - A0, A1
// pwm in on pin 27 - A2 : 220-268Hz, pulse width - .9-4506us, pulse width high
//                        .9 -> 12000, 4506 -> 60,000,000
// quadrature encoder on pins 24, 25 - A3, SDA
// I2c address pins 3, 4; 5, 6

#include <Arduino.h>
#include <EEPROM.h>
#include <Wire.h>
#include <Servo.h>
#include "encoder.h"      // from xrp firmware

#define STARTADDRESS 16   // IN1/2 high 16, in1 low 17, in2 low 18, in1/2 low 19
#define I2CConnector Wire1

#define PWM_OUTPUT1 29    // drive motor
#define PWM_OUTPUT2 28    // turn motor
#define encoder_a   24    // drive encoder a
#define encoder_b   25    // drive encoder b
#define PWM_INPUT   27    // turn dutycycleencoder
#define ADDR_IN1    3
#define ADDR_IN2    5
#define ADDR_OUT1   4
#define ADDR_OUT2   6
#define UPDATE_POS  21    // BOOTSEL button

Servo Servos[2];        // 0 is drive motor, 1 is turn motor
xrp::Encoder encoder;

uint posoffset;
#define VALUEOFFSET   0
#define IVALUEOFFSET  4
uint startupdate;

uint offsetread()
{
  uint value;
  uint valueinvert;
  EEPROM.get(VALUEOFFSET, value);
  EEPROM.get(IVALUEOFFSET, valueinvert);
  if(value == ~valueinvert) {
    Serial.print("EEPROM set, "); Serial.print(value); Serial.println(" used");
    return value;
  }
  else {
    Serial.println("EEPROM not set, 0 used");
    return 0;
  }
}

void offsetwrite(uint value)
{
  if(posoffset != value){
    posoffset = value;
    Serial.print("EEPROM write = "); Serial.println(value);
    EEPROM.put(VALUEOFFSET, value);
    EEPROM.put(IVALUEOFFSET, ~value);
    EEPROM.commit();
  }
}

#define SERVOMIN	 900
#define SERVOZERO	1500
#define SERVOMAX	2100

void setup()
{
  int addr = STARTADDRESS;
  Serial.begin(115200);                             // start serial for output
  //while (!Serial);
  delay(2000);
  Serial.print(F("CPU Frequency = ")); Serial.print(F_CPU / 1000000); Serial.println(F(" MHz"));
  
  // pwm output, 1 is drive motor, 2 is turn motor
  Servos[0].attach(PWM_OUTPUT1, SERVOMIN, SERVOMAX);
  Servos[0].writeMicroseconds(SERVOZERO);
  Servos[1].attach(PWM_OUTPUT2, SERVOMIN, SERVOMAX);
  Servos[1].writeMicroseconds(SERVOZERO);

  // calculate i2c address
  pinMode(ADDR_IN1, INPUT_PULLUP);
  pinMode(ADDR_IN2, INPUT_PULLUP);
  pinMode(ADDR_OUT1, OUTPUT);
  pinMode(ADDR_OUT2, OUTPUT);
  digitalWrite(ADDR_OUT1, LOW);
  digitalWrite(ADDR_OUT2, LOW);
  if (digitalRead(ADDR_IN1) == LOW)
    addr += 1;
  if (digitalRead(ADDR_IN2) == LOW)
    addr += 2;
  Serial.print("address = ");Serial.println(addr);
  
  // quadrature encoder for drive speed
  if(!encoder.init(encoder_a))
    Serial.println("Encoder failed to init");
  else
    encoder.enable();

  // pulse width input for absolute angle encoder
  pinMode(PWM_INPUT, INPUT_PULLUP);
  Serial.print("Started interrupt for digitalPinToInterrupt(pin) = "); Serial.println(digitalPinToInterrupt(PWM_INPUT));
  attachInterrupt(digitalPinToInterrupt(PWM_INPUT), interruptpwm, CHANGE);

  startupdate = 0;
  pinMode(UPDATE_POS, INPUT_PULLUP);
  EEPROM.begin(512);
  posoffset = offsetread();

  // setup i2c device
  I2CConnector.begin(addr);                           // join i2c bus with address #4
  I2CConnector.onReceive(receiveEvent);               // register event
  I2CConnector.onRequest(requestEvent);
}

volatile uint64_t runningwidth;
uint64_t lastrunningwidth;
void loop()
{
  int next = encoder.update();
  if(next >= 8) {
    Serial.print("Encoder Possible PIO RX Buffer Overrun: ");Serial.println(next);
  }
  cli();
  lastrunningwidth = runningwidth;
  sei();
  // if bootsel button is pressed and released, save current PWM width to EEPROM
  if(digitalRead(UPDATE_POS) == LOW){
    if(startupdate == 0)
      startupdate = millis();
  }
  else if(startupdate != 0){
    if((millis()-startupdate) > 1000){
      // button held for more than 1 second and released
      // and current pwm width is different from offset value
      offsetwrite(lastrunningwidth);
    }
    startupdate = 0;
  }
}

uint64_t MINWIDTH =   80LL;
uint64_t MAXWIDTH =   500000LL;
uint64_t DIVIDERCPU = ((uint64_t)F_CPU)/1000000LL;
volatile uint64_t starttime;
void interruptpwm() {
  int in = digitalRead(PWM_INPUT);
  if (in == HIGH)
    starttime = rp2040.getCycleCount64();   // save rising edge time
  else {
    uint64_t pulse_width = (rp2040.getCycleCount64() - starttime)*100LL; // number of cpu clocks * 100, @133Mhz and 0.9-4506us gives 11,970-59,929,800
    pulse_width = pulse_width/DIVIDERCPU;			 	 // 90-450,600
    // > .8us and < 5000us, ignore if outside this range
    if((pulse_width > MINWIDTH) && (pulse_width < MAXWIDTH))
      runningwidth = (runningwidth*7LL + pulse_width)/8LL;
  }
}

uint servovalue(uint x1, uint x2)
{
  return x2 * 256 + x1;
}

// function that executes whenever data is received from master
// this function is registered as an event, see setup()
void receiveEvent(int howMany)
{
  int x1, x2, x;
  if(howMany >= 2){
    x1 = I2CConnector.read();                       // receive byte as an integer
    x2 = I2CConnector.read();                       // receive byte as an integer
    howMany -= 2;
    Servos[0].writeMicroseconds(x=servovalue(x1, x2));// range is 900-2100, 0 -> SERVOMIN, 128 -> SERVOZERO, 255 -> SERVOMAX
    Serial.print("M0:");Serial.println(x);          // print the integer
  }
  if(howMany >= 2){
    x1 = I2CConnector.read();                       // receive byte as an integer
    x2 = I2CConnector.read();                       // receive byte as an integer
    Servos[1].writeMicroseconds(x=servovalue(x1, x2));// range is 900-2100, 0 -> SERVOMIN, 128 -> SERVOZERO, 255 -> SERVOMAX
    Serial.print("M1:");Serial.println(x);          // print the integer
  }
}

void host2net(uint v, byte *ptr){
  ptr[0] = v & 0xff;
  ptr[1] = (v>>8) & 0xff;
  ptr[2] = (v>>16) & 0xff;
  ptr[3] = (v>>24) & 0xff;
}

// return encoder and pwm pulse width
void requestEvent()
{
  byte val[20];
  int encodercount = encoder.getCount();
  int encoderperiod = encoder.getPeriod();
  int encoderdivisor = F_CPU / encoder2_CYCLES_PER_COUNT;
  int width = lastrunningwidth;
  if(posoffset != 0) {
    width -= posoffset;
    width += 90;
    if(width < 0)
      width += 450600;
    if((width < 90) || (width > 450600))
      width = 450600;
  }
  //Serial.print("E:");Serial.print(encodercount);Serial.print(", P:");Serial.print(width);Serial.print(", ");Serial.println(posoffset);
  host2net(encodercount, &val[0]);
  host2net(encoderperiod, &val[4]);
  host2net(encoderdivisor, &val[8]);
  host2net(width, &val[12]);
  host2net(posoffset, &val[16]);
  I2CConnector.write(val, 20);
}

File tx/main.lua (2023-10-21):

local WGTNAME = "Swerve" .. "0.9"  -- max 9 characters

--[[
HISTORY
=======
Based on Author Mike Shellim http://www.rc-soar.com/opentx/lua

2023-07-26  v0.1.0 	First release

DESCRIPTION
===========
Displays basic info about active model.
At startup looks for output named 'armed'. If found, flashes
  'motor armed' when output value > 0.

REQUIREMENTS
============
Transmitter with colour screen (X10, X12, T16 etc.)
OpenTX v 2.2 or later

INSTRUCTIONS
============
Please read instructions in the zip package, or download from :
https://rc-soar.com/opentx/lua/showitall/ShowItAll_09.pdf


DISCLAIMER
==========
CHECK FOR CORRECT OPERATION BEFORE USE. IF IN DOUBT DO NOT FLY!!

USER SETTABLE VARIABLES
=======================
MAX_LS = maximum number of logical switches to display
A value of 20 is recommended for good performance in general use
If not using other scripts, you can increase this value
to a suggested max of 32 --]]

local MAX_LS = 20

--[[
SHOW_UNDEF_LS_AS_DOT determines how undefined logical switches
are rendered
If false (default), undefined logical switches are treated as 'off'.
If true, then undefined ls's are rendered as dots (nice!), but involves a cache
look up and a power cycle to refresh cache - best used only if logical switches
have been finalised.
 --]]

local SHOW_UNDEF_LS_AS_DOT = false

--[[
END OF USER SETTABLE VARIABLES
============================== --]]


-- ========= LOCAL VARIABLES =============
-- Field ids
local idSA
local idTmr1
local idLS1
local idTxV
local idEle
local idAil
local idRud
local idThr
local idchArmed
local idCh1
local strVer

-- voltage telemetry sensors in priority order
local batsens = {"Cels", "RxBt", "A1", "A2", "A3", "A4"}

-- item counts
local nLS
local nTmr

-- options table
local defaultOptions = {
	{"Use dflt clrs", BOOL, 1},
	{"BackColor", COLOR, WHITE},
	{"ForeColor", COLOR, BLACK},
	}
local colorFlags
local sticks = {}

-- Logical switch bitmap
local LSDefLo -- bitmap of definition state for LS's 0-31
local LSDefHi -- bitmap of definition state for LS's 32-63

-- fonts
local fontht = {[SMLSIZE]=12, [0]=18}

-- ========= S T A R T   O F   F U N C T I O N S =============

--[[
FUNCTION: initLSDefs
Populate logical switch bitmap cache. 1=defined, 0=undefined
(Cache needed as getLogicalSwitch is slow.)
--]]
local function initLSDefs ()
	LSDefLo = 0
	LSDefHi = 0
	for i = 0, 31 do
		local vLo = (model.getLogicalSwitch(i).func > 0) and 1 or 0
		local vHi = (model.getLogicalSwitch(i+32).func >0) and 1 or 0
		LSDefLo = bit32.replace (LSDefLo, vLo, i)
		LSDefHi = bit32.replace (LSDefHi, vHi, i)
	end
end

--[[
FUNCTION: getLSVal
Returns logical switch value or nil
Nil = undefined
1024 = true
-1024 = false
If SHOW_UNDEF_LS_AS_DOT is false, then undefined LS's will be treated as false
--]]
local function getLSVal (i)
	local val = getValue (idLS1 + i)
	if SHOW_UNDEF_LS_AS_DOT then
		local long = i>31 and LSDefHi or LSDefLo
		if bit32.extract (long, i%32) == 0 then
			val = nil
		end
	end
	return val
end

--[[
FUNCTION: getNumItems
Determine the number of items in a field
--]]
local function getNumItems (field, maxitems)
	local i = 1
	while true do
		if i > maxitems or not getFieldInfo(field ..i) then
			break
		end
		i = i + 1
	end
	return i-1
end

--[[
==================================================
FUNCTION: create
Called by OpenTX to create the widget
==================================================
--]]

local function create(zone, options)

	-- stash field id's (efficiency)
	idSA = getFieldInfo('sa').id
	idLS1 = getFieldInfo('ls1').id
	idTmr1 = getFieldInfo('timer1').id
	idTxV = getFieldInfo('tx-voltage').id
	idEle= getFieldInfo('ele').id
	idAil= getFieldInfo('ail').id
	idRud= getFieldInfo('rud').id
	idThr= getFieldInfo('thr').id
	idCh1 = getFieldInfo('ch1').id

	local _, _, major, minor, rev, osname = getVersion()
	strVer = (osname or "OpenTX") .. " " .. major .. "." .. minor.. "." .. rev


	-- Limit LS count to avoid possible performance
	-- hit especially with mixer scripts.
	nLS = getNumItems ('ls', MAX_LS)
	nTmr = getNumItems ('timer',3)

	-- Initialise LS bitmap
	initLSDefs ()

	-- look for output channel named 'armed'
	idchArmed = nil
	local i = 0
	while true do
		local o = model.getOutput (i)
		if not o then break end
		if string.lower (string.sub (o.name, 1,5)) == "armed" then
			idchArmed = getFieldInfo ("ch".. (i+1)).id
			break
		end
		i = i + 1
	end

	sticks={
		{name='A', id=idAil},
		{name='E', id=idEle},
		{name='T', id=idThr},
		{name='R', id=idRud}
		}

	return {zone=zone, options=options}
end


--[[
==================================================
FUNCTION: update
Called by OpenTX on registration and at
change of settings
==================================================
--]]
local function update(wgt, newOptions)
    wgt.options = newOptions
end

--[[
==================================================
FUNCTION: background
Periodically called by OpenTX
==================================================
--]]
local function background(wgt)
end


--[[
FUNCTION: hms
Convert time in seconds into string [-]hh:mm:ss
--]]
local function hms (n)

	local stSign
	if n < 0 then
		stSign = "-"
		n = -n
	else
		stSign = " "
	end

	local hh = math.floor (n/3600)
	n = n % 3600
	local mm = math.floor (n/60)
	local ss = n % 60

	-- replacement for buggy string.format()
	-- https://github.com/opentx/opentx/issues/6201
	local function fmt (v)
		return #(v .. "") >=2 and v or ("0" ..v)
	end
	return stSign .. fmt(hh) .. ':' .. fmt(mm) .. ':' .. fmt(ss)
end




--[[
FUNCTION: drawSwitchSymbol
Draw a symobol representing switch state up/middle/down
--]]
local function drawSwitchSymbol (x,y,val)
	local w=5
	local h=8
	local weight = 2
	if val==0 then
		lcd.drawFilledRectangle (x, y+h/2, w,1, colorFlags)
	elseif val > 0 then
		lcd.drawFilledRectangle (x+ w/2, y+h/2-1, 1,h/2+1,colorFlags)
		lcd.drawFilledRectangle (x, y+h, w,weight,colorFlags)
	else
		lcd.drawFilledRectangle (x+ w/2, y, 1,h/2+2,colorFlags)
		lcd.drawFilledRectangle (x, y, w,weight,colorFlags)
	end
end

--[[
FUNCTION: drawSwitches
Draw switch block
--]]
local function drawSwitches (x,y)
	-- Switches
	local x0 = x
	local y0 = y
	for i = 0, 7 do
		lcd.drawText (x, y, "S".. string.char(string.byte('A')+i), SMLSIZE + colorFlags)
		drawSwitchSymbol (x+22, y+4, getValue (idSA+i))
		y = y + 12
		if i==3 then
			x = x0 + 40
			y = y0
		end
	end
end

--[[
FUNCTION: drawFM
Display flight mode
--]]
local function drawFM (x,y, font)
	local fmno, fmname = getFlightMode()
	if fmname == "" then
		fmname = "FM".. fmno
	end
	lcd.drawText (x, y, fmname, font + colorFlags)
end
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

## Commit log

2023-07-13 setting motor direction and pid constants
2023-07-18 osh version
    [swerve1.kicad_pcb, swerve1.kicad_sch]
2023-07-18 schematic and render of boards
    [swerve1.kicad_pcb]
2023-07-26 update pcb
    [swerve.kicad_pcb, swerve.kicad_sch]
2023-07-26 sport working, quadrature encoder update
2023-07-28 updated pcb
    [swerve.kicad_pcb, swerve1.kicad_pcb, swerve1.kicad_sch]
2023-07-28 optical flow telemetry
2023-07-29 flowx,y working
2023-07-29 use throttle to limit speed
2023-07-30 make velocity period configurable
2023-07-30 add encoder speed
2023-07-30 correct wheel position
2023-07-30 battery voltage and barometric telemetry
2023-08-02 pcb backup
2023-08-03 add battery cell telemetry
2023-08-03 speed up i2c bus
2023-08-04 fix telemetry on motorstop and comments
2023-08-07 brake and i2c speed changes
2023-08-07 i2c bus speed
2023-08-07 voltage telemetry fixes
2023-08-07 skipping stopping on min battery if
2023-08-13 controlled fan
2023-08-13 debug logical and real pin offsets
2023-08-13 fan test routine
2023-08-13 controlled motor fan
2023-08-13 battery/temp telemetry, config for motor connection changes
2023-08-13 denoise temp ADC sensor
2023-08-13 denoise temp sensor, correct battery ratio
2023-08-15 fan on/off and license
2023-08-15 remove adc test code, rc channel to switch pid update
2023-08-16 led always to bitmask
2023-08-16 comments, maxangle, pid constants
2023-08-16 del kicad baclups
2023-08-16 correct pcb directories
    [swerve1.kicad_pcb, swerve1.kicad_sch]
2023-08-16 using pcb
2023-08-17 missed inverting 2 drive motors
2023-08-30 add bom
2023-10-07 add lidar and nn
2023-10-07 integration lidar for autoroam
2023-10-09 move battery config to separate file
2023-10-09 enable gps, lidar, etc
2023-10-09 use 8 lidar and x/y/r as input, new weights
2023-10-09 Update swervebot.spin2
    battery to separate file
    temp limits
    sensor loop count
    nn test
2023-10-10 lidar found
2023-10-10 lidar fixes
2023-10-17 i2c device for 8 pwm outputs
2023-10-17 revert spi change
2023-10-17 use new motordriver
2023-10-17 driver for i2c pwm device
2023-10-18 added support for qt-py board
2023-10-21 fix motor invert
2023-10-21 correct offsets, inverts and pid tuning for new esv
2023-10-21 correct motor stop value
2024-07-04 Create swerve_driver.ino
    new swerve module driver
2024-07-28 i2c scanner for pico
    When electronics is using pico-w
2024-07-28 rp2040 qt py
    Code for rp2040 qt py to control 1 swerve module - motor driver, encoder, angle sensor. Available to main pico-w as a i2c device.
2024-07-29 motor control to uint16 width
2025-04-30 updated to use release xrp board
